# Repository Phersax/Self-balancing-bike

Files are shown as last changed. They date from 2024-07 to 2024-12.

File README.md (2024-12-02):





## About the Project
This project involves the development of a self-balancing bicycle designed to remain stable in
a stationary position on a flat surface. The balance is autonomously maintained through a
reaction wheel powered by a motor, whose controlled movement counteracts the bicycle’s tilt.
For small tilt angles, the system can be approximated as an inverted pendulum.
The structure was created using 3D printing and then assembled, following a preliminary modeling phase in SolidWorks.

The control system relies on precise timing: A main timer manages a callback triggered at
defined time intervals, while a second timer regulates the generation of the PWM signal needed
to control the motor. An additional timer has been set up for reading the encoder data. As for
the data from the IMU, it is acquired via the I2C protocol.

The control model is structured with two loops. The inner loop uses encoder data to implement
closed-loop speed control, while the outer loop relies on IMU readings to adjust the position.
To achieve an accurate angle reading, sensor data fusion has been implemented through a filter
that combines information from an MPU6050 IMU, equipped with an integrated accelerometer
and gyroscope.

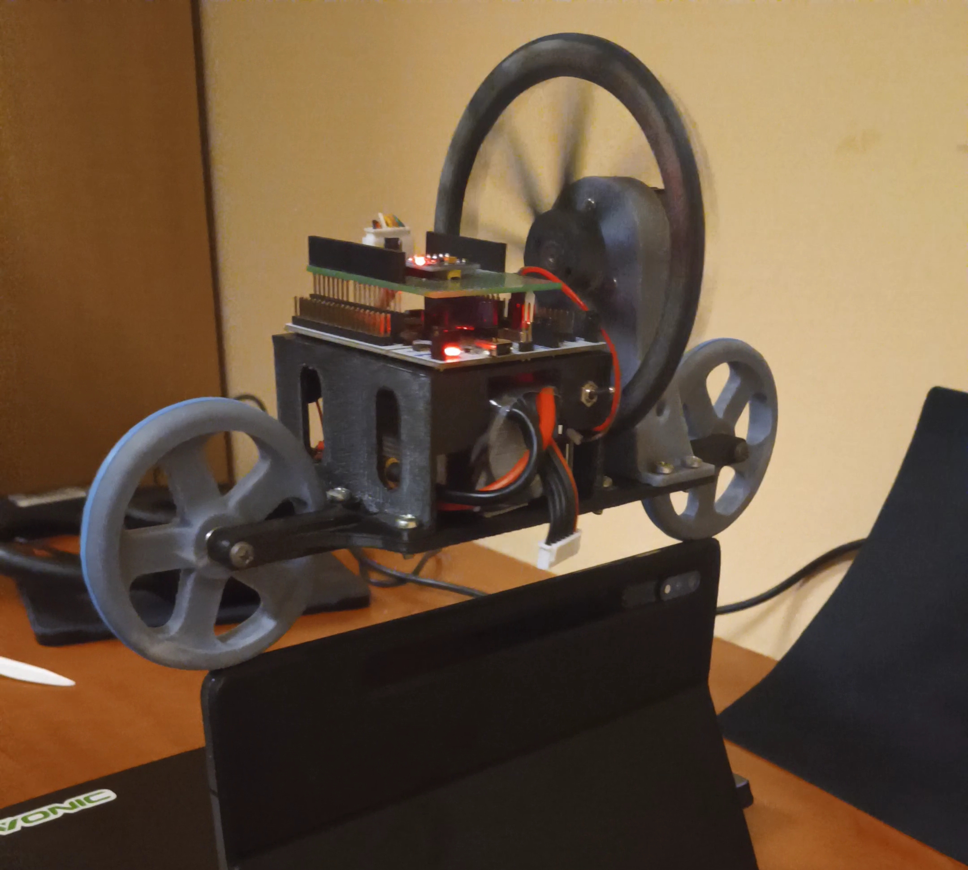
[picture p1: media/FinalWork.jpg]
Final Overview


## Schematic
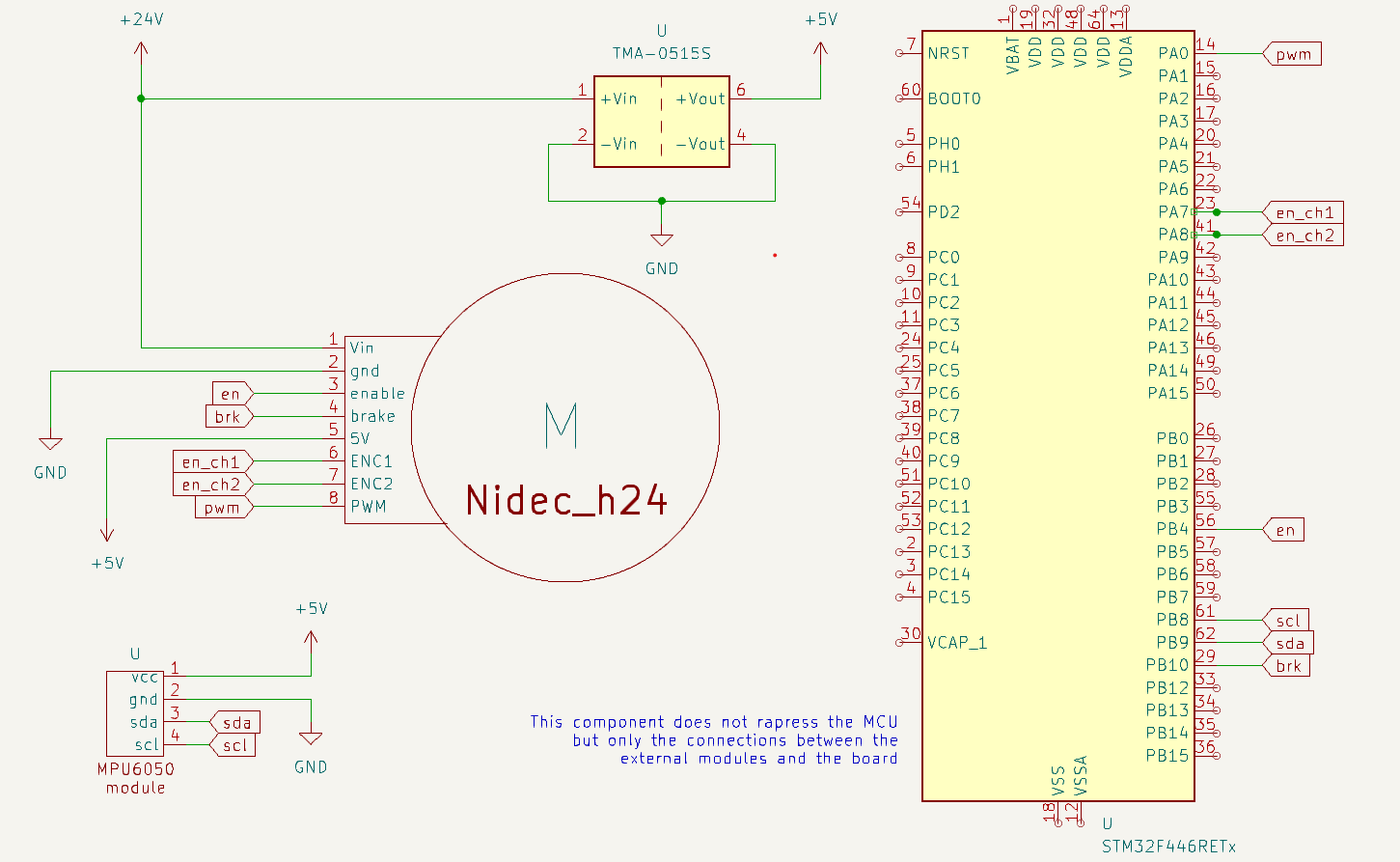
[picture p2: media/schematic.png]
Schematic


## Additional info
Check out the report if you are interested in our work!

[Link to the report](SELF_BALANCING_BIKE_REPORT.pdf)

[Link to the pinout and configuration](pinout_and_config_report.pdf)

🚀 Happy coding! 🌟

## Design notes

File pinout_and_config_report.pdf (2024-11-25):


25/11/2024

main Project
Configuration Report

## 1. Description

### 1.1. Project

Project Name | main
Board Name | custom
Generated with: | STM32CubeMX 6.12.1
Date | 11/25/2024

### 1.2. MCU

MCU Series | STM32F4
MCU Line | STM32F446
MCU name | STM32F446RETx
MCU Package | LQFP64
MCU Pin number | 64

### 1.3. Core(s) information

Core(s) | Arm Cortex-M4

## 2. Pinout Configuration

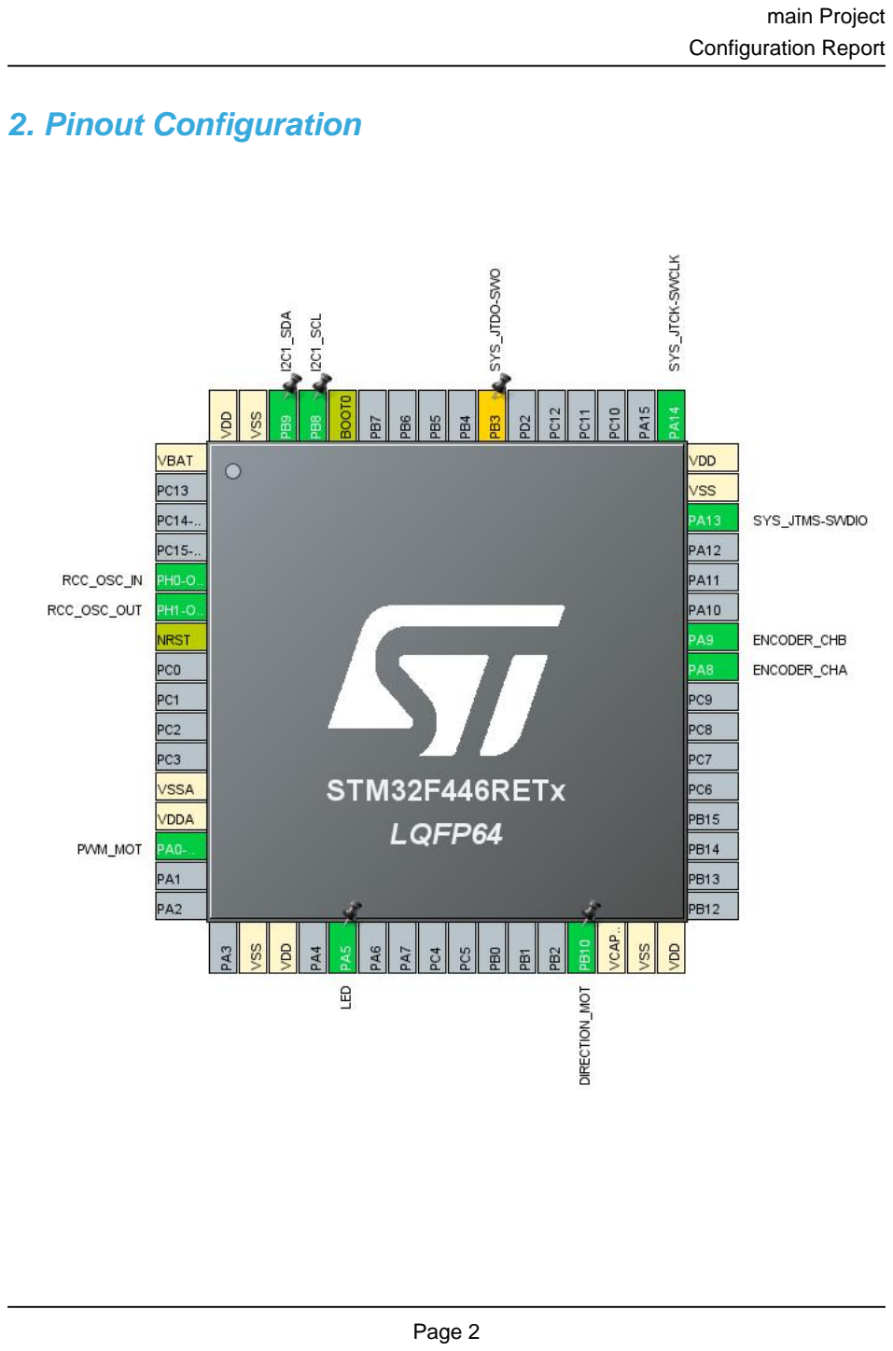
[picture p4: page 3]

## 3. Pins Configuration

Pin Number LQFP64 | Pin Name (function after reset) | Pin Type | Alternate Function(s) | Label
1 | VBAT | Power
5 | PH0-OSC_IN | I/O | RCC_OSC_IN
6 | PH1-OSC_OUT | I/O | RCC_OSC_OUT
7 | NRST | Reset
12 | VSSA | Power
13 | VDDA | Power
14 | PA0-WKUP | I/O | TIM5_CH1 | PWM_MOT
18 | VSS | Power
19 | VDD | Power
21 | PA5 * | I/O | GPIO_Output | LED
29 | PB10 * | I/O | GPIO_Output | DIRECTION_MOT
30 | VCAP_1 | Power
31 | VSS | Power
32 | VDD | Power
41 | PA8 | I/O | TIM1_CH1 | ENCODER_CHA
42 | PA9 | I/O | TIM1_CH2 | ENCODER_CHB
46 | PA13 | I/O | SYS_JTMS-SWDIO
47 | VSS | Power
48 | VDD | Power
49 | PA14 | I/O | SYS_JTCK-SWCLK
55 | PB3 ** | I/O | SYS_JTDO-SWO
60 | BOOT0 | Boot
61 | PB8 | I/O | I2C1_SCL
62 | PB9 | I/O | I2C1_SDA
63 | VSS | Power
64 | VDD | Power

* The pin is affected with an I/O function
** The pin is affected with a peripheral function but no peripheral mode is activated

## 4. Clock Tree Configuration

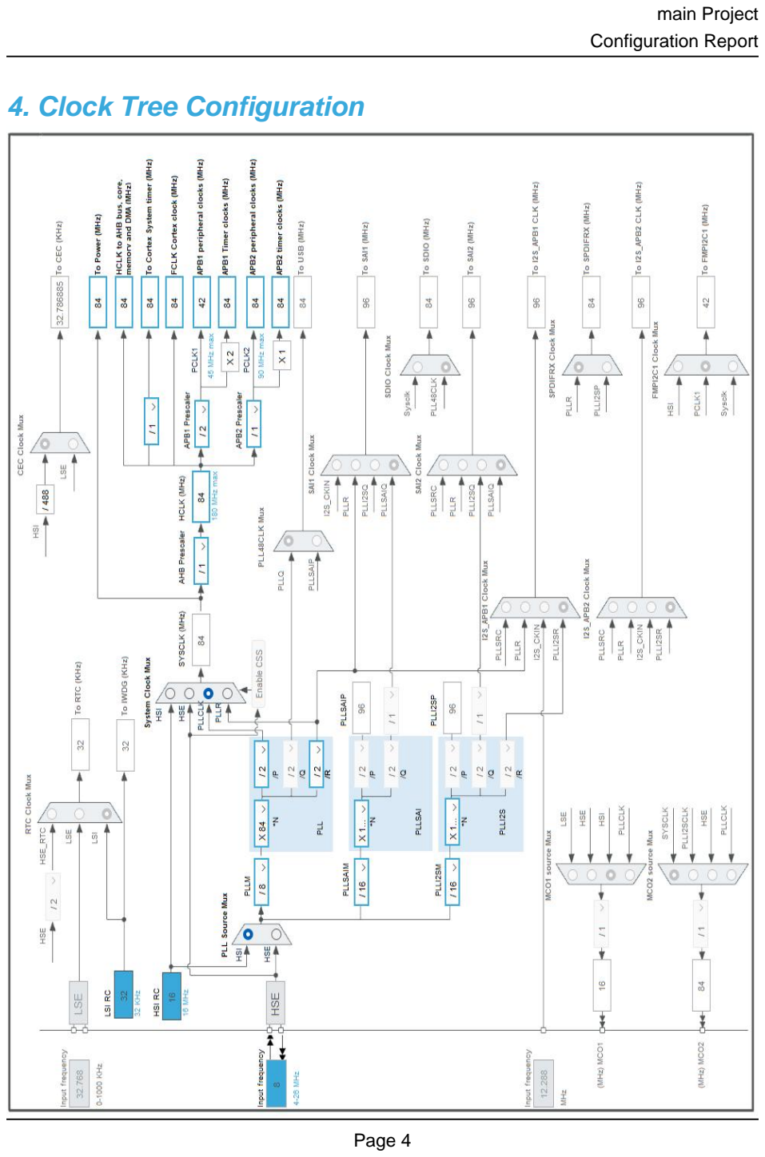
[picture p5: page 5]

## 1. Power Consumption Calculator report

### 1.1. Microcontroller Selection

Series | STM32F4
Line | STM32F446
MCU | STM32F446RETx
Datasheet | DS10693_Rev6

### 1.2. Parameter Selection

Temperature | 25
Vdd | 3.3

### 1.3. Battery Selection

Battery | Li-SOCL2(A3400)
Capacity | 3400.0 mAh
Self Discharge | 0.08 %/month
Nominal Voltage | 3.6 V
Max Cont Current | 100.0 mA
Max Pulse Current | 200.0 mA
Cells in series | 1
Cells in parallel | 1

### 1.4. Sequence

Step | Step1 | Step2
Mode | RUN | STOP_UDM (Under Drive)
Vdd | 3.3 | 3.3
Voltage Source | Battery | Battery
Range | Scale1-High | No Scale
Fetch Type | RAM/FLASH/REGON/ART/P REFETCH | n/a
CPU Frequency | 180 MHz | 0 Hz
Clock Configuration | HSE PLL | Regulator_LP Flash-PwrDwn
Clock Source Frequency | 4 MHz | 0 Hz
Peripherals
Additional Cons. | 0 mA | 0 mA
Average Current | 46 mA | 55 µA
Duration | 0.1 ms | 0.9 ms
DMIPS | 225.0 | 0.0
Ta Max | 98.02 | 104.99
Category | In DS Table | In DS Table

### 1.5. Results

Sequence Time | 1 ms | Average Current | 4.65 mA
Battery Life | 1 month | Average DMIPS | 225.0 DMIPS

### 1.6. Chart

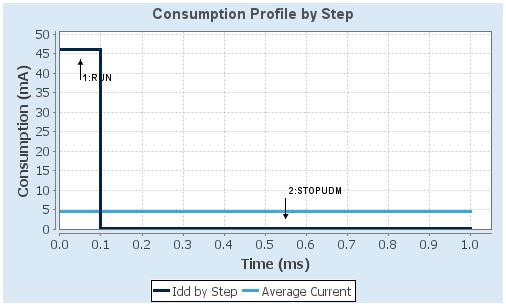
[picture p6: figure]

## 2. Software Project

### 2.1. Project Settings

Name | Value
Project Name | main
Project Folder | C:\Users\Francesco Stasi\OneDrive - Politecnico di
Toolchain / IDE | STM32CubeIDE
Firmware Package Name and Version | STM32Cube FW_F4 V1.28.1
Application Structure | Advanced
Generate Under Root | Yes
Do not generate the main() | No
Minimum Heap Size | 0x200
Minimum Stack Size | 0x400

### 2.2. Code Generation Settings

Name | Value
STM32Cube MCU packages and embedded software | Copy only the necessary library files
Generate peripheral initialization as a pair of '.c/.h' files | Yes
Backup previously generated files when re-generating | No
Keep User Code when re-generating | Yes
Delete previously generated files when not re-generated | Yes
Set all free pins as analog (to optimize the power consumption) | No
Enable Full Assert | No

### 2.3. Advanced Settings - Generated Function Calls

Rank | Function Name | Peripheral Instance Name
1 | SystemClock_Config | RCC
2 | MX_GPIO_Init | GPIO
3 | MX_TIM5_Init | TIM5
4 | MX_I2C1_Init | I2C1
5 | MX_TIM1_Init | TIM1
6 | MX_TIM2_Init | TIM2

## 3. Peripherals and Middlewares Configuration

### 3.1. I2C1

I2C: I2C
3.1.1. Parameter Settings:

Master Features:

I2C Speed Mode | Fast Mode *
I2C Clock Speed (Hz) | 400000
Fast Mode Duty Cycle | Duty cycle Tlow/Thigh = 2
Slave Features:
Clock No Stretch Mode | Disabled
Primary Address Length selection | 7-bit
Dual Address Acknowledged | Disabled
Primary slave address | 0
General Call address detection | Disabled

### 3.2. RCC

High Speed Clock (HSE): Crystal/Ceramic Resonator
3.2.1. Parameter Settings:

System Parameters:

VDD voltage (V) | 3.3
Instruction Cache | Enabled
Prefetch Buffer | Enabled
Data Cache | Enabled
Flash Latency(WS) | 2 WS (3 CPU cycle)
RCC Parameters:
HSI Calibration Value | 16
TIM Prescaler Selection | Disabled
HSE Startup Timout Value (ms) | 100
LSE Startup Timout Value (ms) | 5000
Power Parameters:
Power Regulator Voltage Scale | Power Regulator Voltage Scale 3
Power Over Drive | Disabled

### 3.3. SYS

Debug: Serial Wire
Timebase Source: SysTick

### 3.4. TIM1

Combined Channels: Encoder Mode
3.4.1. Parameter Settings:

Counter Settings:

Prescaler (PSC - 16 bits value) | 0
Counter Mode | Up
Counter Period (AutoReload Register - 16 bits value ) | 65535
Internal Clock Division (CKD) | No Division
Repetition Counter (RCR - 8 bits value) | 0
auto-reload preload | Disable
Trigger Output (TRGO) Parameters:
Master/Slave Mode (MSM bit) | Disable (Trigger input effect not delayed)
Trigger Event Selection | Reset (UG bit from TIMx_EGR)
Encoder:
Encoder Mode | Encoder Mode TI1 and TI2 *

____ Parameters for Channel 1 ____
Polarity | Rising Edge
IC Selection | Direct
Prescaler Division Ratio | No division
Input Filter | 0
____ Parameters for Channel 2 ____
Polarity | Rising Edge
IC Selection | Direct
Prescaler Division Ratio | No division
Input Filter | 0

### 3.5. TIM2

Clock Source : Internal Clock
3.5.1. Parameter Settings:

Counter Settings:

Prescaler (PSC - 16 bits value) | 0
Counter Mode | Up

Counter Period (AutoReload Register - 32 bits value ) | 336000-1 *
Internal Clock Division (CKD) | No Division
auto-reload preload | Disable
Trigger Output (TRGO) Parameters:
Master/Slave Mode (MSM bit) | Disable (Trigger input effect not delayed)
Trigger Event Selection | Reset (UG bit from TIMx_EGR)

### 3.6. TIM5

Channel1: PWM Generation CH1
3.6.1. Parameter Settings:

Counter Settings:

Prescaler (PSC - 16 bits value) | 0
Counter Mode | Up
Counter Period (AutoReload Register - 32 bits value ) | 4199 *
Internal Clock Division (CKD) | No Division
auto-reload preload | Enable *
Trigger Output (TRGO) Parameters:
Master/Slave Mode (MSM bit) | Disable (Trigger input effect not delayed)
Trigger Event Selection | Reset (UG bit from TIMx_EGR)
PWM Generation Channel 1:
Mode | PWM mode 1
Pulse (32 bits value) | 0
Output compare preload | Enable
Fast Mode | Disable
CH Polarity | High

* User modified value

## 4. System Configuration

### 4.1. GPIO configuration

IP | Pin | Signal | GPIO mode | GPIO pull/up pull down | Max Speed | User Label
I2C1 | PB8 | I2C1_SCL | Alternate Function Open Drain | Pull-up * | Very High *
| PB9 | I2C1_SDA | Alternate Function Open Drain | Pull-up * | Very High *
RCC | PH0-OSC_IN | RCC_OSC_IN | n/a | n/a | n/a
| PH1-OSC_OUT | RCC_OSC_OUT | n/a | n/a | n/a
SYS | PA13 | SYS_JTMS-SWDIO | n/a | n/a | n/a
| PA14 | SYS_JTCK-SWCLK | n/a | n/a | n/a
TIM1 | PA8 | TIM1_CH1 | Alternate Function Push Pull | Pull-up * | Low | ENCODER_CHA
| PA9 | TIM1_CH2 | Alternate Function Push Pull | Pull-up * | Low | ENCODER_CHB
TIM5 | PA0-WKUP | TIM5_CH1 | Alternate Function Push Pull | No pull-up and no pull-down | Low | PWM_MOT
Single Mapped Signals | PB3 | SYS_JTDO-SWO | n/a | n/a | n/a
GPIO | PA5 | GPIO_Output | Output Push Pull | No pull-up and no pull-down | Low | LED
| PB10 | GPIO_Output | Output Push Pull | Pull-down * | Low | DIRECTION_MOT

### 4.2. DMA configuration

nothing configured in DMA service

### 4.3. NVIC configuration

4.3.1. NVIC
Interrupt Table | Enable | Preenmption Priority | SubPriority
Non maskable interrupt | true | 0 | 0
Hard fault interrupt | true | 0 | 0
Memory management fault | true | 0 | 0
Pre-fetch fault, memory access fault | true | 0 | 0
Undefined instruction or illegal state | true | 0 | 0
System service call via SWI instruction | true | 0 | 0
Debug monitor | true | 0 | 0
Pendable request for system service | true | 0 | 0
System tick timer | true | 15 | 0
TIM2 global interrupt | true | 0 | 0
PVD interrupt through EXTI line 16 | unused
Flash global interrupt | unused
RCC global interrupt | unused
TIM1 break interrupt and TIM9 global interrupt | unused
TIM1 update interrupt and TIM10 global interrupt | unused
TIM1 trigger and commutation interrupts and TIM11 global interrupt | unused
TIM1 capture compare interrupt | unused
I2C1 event interrupt | unused
I2C1 error interrupt | unused
TIM5 global interrupt | unused
FPU global interrupt | unused
4.3.2. NVIC Code generation
Enabled interrupt Table | Select for init sequence ordering | Generate IRQ handler | Call HAL handler
Non maskable interrupt | false | true | false
Hard fault interrupt | false | true | false
Memory management fault | false | true | false
Pre-fetch fault, memory access fault | false | true | false
Undefined instruction or illegal state | false | true | false
System service call via SWI instruction | false | true | false
Debug monitor | false | true | false
Pendable request for system service | false | true | false
System tick timer | false | true | true
TIM2 global interrupt | false | true | true

* User modified value

## 5. System Views

5.1. Category view
5.1.1. Current

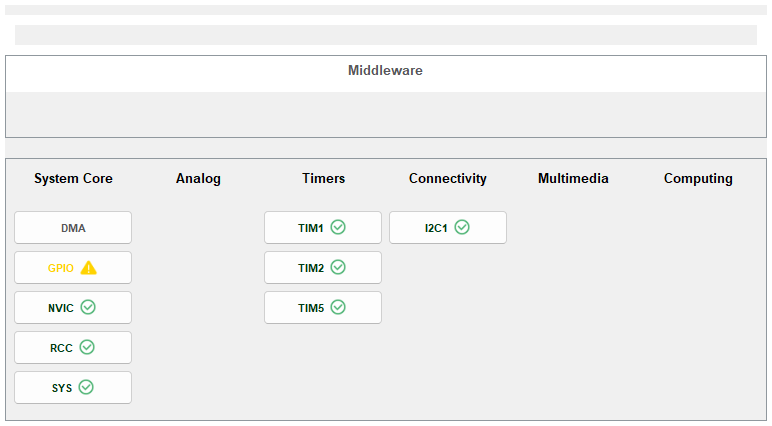
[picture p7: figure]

## 6. Docs & Resources

Type | Link
BSDL files | https://www.st.com/resource/en/bsdl_model/stm32f446_bsdl.zip
IBIS models | https://www.st.com/resource/en/ibis_model/stm32f446_ibis.zip
System View Description | https://www.st.com/resource/en/svd/stm32f4-svd.zip
Presentations | https://www.st.com/resource/en/product_presentation/stm32-stm8_embedded_software_solutions.pdf
Presentations | https://www.st.com/resource/en/product_presentation/stm32_eval-tools_portfolio.pdf
Presentations | https://www.st.com/resource/en/product_presentation/stm32_stm8_functi onal-safety-packages.pdf
Presentations | https://www.st.com/resource/en/product_presentation/stm32-stm8_software_development_tools.pdf
Presentations | https://www.st.com/resource/en/product_presentation/microcontrollers-stm32-family-overview.pdf
Presentations | https://www.st.com/resource/en/product_presentation/microcontrollers-stm32h7rs-lines-overview.pdf
Brochures | https://www.st.com/resource/en/brochure/products-and-solutions-for-plcs-and-smart-i-os.pdf
Flyers | https://www.st.com/resource/en/flyer/flstm32nucleo.pdf
Flyers | https://www.st.com/resource/en/flyer/flstmcsuite.pdf
Flyers | https://www.st.com/resource/en/flyer/flstm32trust.pdf
Product Certifications | https://www.st.com/resource/en/certification_document/stm32_authentication_can.pdf
Application Notes | https://www.st.com/resource/en/application_note/an1709-emc-design-guide-for-stm8-stm32-and-legacy-mcus-stmicroelectronics.pdf
Application Notes | https://www.st.com/resource/en/application_note/an2606-stm32-microcontroller-system-memory-boot-mode-stmicroelectronics.pdf
Application Notes | https://www.st.com/resource/en/application_note/an2639-soldering- recommendations-and-package-information-for-leadfree-ecopack-mcus-

| and-mpus-stmicroelectronics.pdf
Application Notes | https://www.st.com/resource/en/application_note/an2945-stm8s-and-stm32-mcus-a-consistent-832bit-product-line-for-painless-migration-stmicroelectronics.pdf
Application Notes | https://www.st.com/resource/en/application_note/an3070-managing-the-driver-enable-signal-for-rs485-and-iolink-communications-with-the-stm32s-usart-stmicroelectronics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
Application Notes | https://www.st.com/resource/en/application_note/an3126-audio-and-waveform-generation-using-the-dac-in-stm32-products-stmicroelectronics.pdf
Application Notes | https://www.st.com/resource/en/application_note/an3154-can-protocol-used-in-the-stm32-bootloader-stmicroelectronics.pdf
Application Notes | https://www.st.com/resource/en/application_note/an3155-usart-protocol-used-in-the-stm32-bootloader-stmicroelectronics.pdf
Application Notes | https://www.st.com/resource/en/application_note/an3156-usb-dfu-protocol-used-in-the-stm32-bootloader-stmicroelectronics.pdf
Application Notes | https://www.st.com/resource/en/application_note/an3364-migration-and-compatibility-guidelines-for-stm32-microcontroller-applications-stmicroelectronics.pdf
Application Notes | https://www.st.com/resource/en/application_note/an3997-audio-playback-and-recording-using-the-stm32f4discovery-stmicroelectronics.pdf
Application Notes | https://www.st.com/resource/en/application_note/an3998-pdm-audio-software-decoding-on-stm32-microcontrollers-stmicroelectronics.pdf
Application Notes | https://www.st.com/resource/en/application_note/an4031-using-the-stm32f2-stm32f4-and-stm32f7-series-dma-controller-stmicroelectronics.pdf
Application Notes | https://www.st.com/resource/en/application_note/an4221-i2c-protocol-used-in-the-stm32-bootloader-stmicroelectronics.pdf
Application Notes | https://www.st.com/resource/en/application_note/an4229-how-to-implement-a-vocoder-solution-using-stm32-microcontrollers-stmicroelectronics.pdf
Application Notes | https://www.st.com/resource/en/application_note/an4286-spi-protocol-used-in-the-stm32-bootloader-stmicroelectronics.pdf

Application Notes | https://www.st.com/resource/en/application_note/an4488-getting-started-with-stm32f4xxxx-mcu-hardware-development-stmicroelectronics.pdf
Application Notes | https://www.st.com/resource/en/application_note/an4566-extending-the-dac-performance-of-stm32-microcontrollers-stmicroelectronics.pdf
Application Notes | https://www.st.com/resource/en/application_note/an4640-peripherals-interconnections-on-stm32f4057xx-stm32f4157xx-stm32f42xxx-stm32f43xxx-stm32f446xx-and-stm32f469479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
Application Notes | https://www.st.com/resource/en/application_note/an4655-virtually-increasing-the-number-of-serial-communication-peripherals-in-stm32-applications-stmicroelectronics.p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
Application Notes | https://www.st.com/resource/en/application_note/an4658-migration-of-applications-from-stm32f429439-lines-to-stm32f446-line-stmicroelectronics.pdf
Application Notes | https://www.st.com/resource/en/application_note/an4739-stm32cube-firmware-examples-for-stm32f4-series-stmicroelectronics.pdf
Application Notes | https://www.st.com/resource/en/application_note/an4750-handling-of-soft-errors-in-stm32-applications-stmicroelectronics.pdf
Application Notes | https://www.st.com/resource/en/application_note/an4776-generalpurpose-timer-cookbook-for-stm32-microcontrollers-stmicroelectronics.pdf
Application Notes | https://www.st.com/resource/en/application_note/an4803-highspeed-si-simulations-using-ibis-and-boardlevel-simulations-using-hyperlynx-si-on-stm32-mcus-and-mpus-stmic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
Application Notes | https://www.st.com/resource/en/application_note/an4850-stm32-mcus-spreadspectrum-clock-generation-principles-properties-and-implementation-stmicroelectronics.pdf
Application Notes | https://www.st.com/resource/en/application_note/an4989-stm32-microcontroller-debug-toolbox-stmicroelectronics.pdf
Application Notes | https://www.st.com/resource/en/application_note/an4995-using-an-electromyogram-technique-to-detect-muscle-activity-stmicroelectronics.pdf
Application Notes | https://www.st.com/resource/en/application_note/an5020-digital-camera-interface-dcmi-on-stm32-mcus-stmicroelectronics.pdf
Application Notes | https://www.st.com/resource/en/application_note/an5027-interfacing-pdm-

| digital-microphones-using-stm32-mcus-and-mpus-stmicroelectronics.pdf
Application Notes | https://www.st.com/resource/en/application_note/an5073-receiving-spdif-audio-stream-with-the-stm32f4f7h7-series-stmicroelectronics.pdf
Application Notes | https://www.st.com/resource/en/application_note/an4760-quadspi-interface-on-stm32-microcontrollers-and-microprocessors--stmicroelectronics.pdf
Application Notes | https://www.st.com/resource/en/application_note/an4899-stm32-microcontroller-gpio-hardware-settings-and-lowpower-consumption-stmicroelectronics.pdf
Application Notes | https://www.st.com/resource/en/application_note/an5612-esd-protection-of-stm32-mcus-and-mpus-stmicroelectronics.pdf
Application Notes | https://www.st.com/resource/en/application_note/an4838-introduction-to-memory-protection-unit-management-on-stm32-mcus-stmicroelectronics.pdf
Application Notes | https://www.st.com/resource/en/application_note/an4879-introduction-to-usb-hardware-and-pcb-guidelines-using-stm32-mcus-stmicroelectronics.pdf
Application Notes | https://www.st.com/resource/en/application_note/an5225-introduction-to-usb-typec-power-delivery-for-stm32-mcus-and-mpus-stmicroelectronics.pdf
Application Notes | https://www.st.com/resource/en/application_note/an2834-how-to-optimize-the-adc-accuracy-in-the-stm32-mcus-stmicroelectronics.pdf
Application Notes | https://www.st.com/resource/en/application_note/an5537-how-to-use-adc-oversampling-techniques-to-improve-signaltonoise-ratio-on-stm32-mcus-stmicroelectronics.pdf
Application Notes | https://www.st.com/resource/en/application_note/an5036-guidelines-for-thermal-management-on-stm32-applications-stmicroelectronics.pdf
Application Notes | https://www.st.com/resource/en/application_note/an4230-introduction-to-random-number-generation-validation-using-the-nist-statistical-test-suite-for-stm32-mcus-and-m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
Application Notes | https://www.st.com/resource/en/application_note/an2867-guidelines-for-oscillator-design-on-stm8afals-and-stm32-mcusmpus-stmicroelectronics.pdf

Application Notes | https://www.st.com/resource/en/application_note/an4013-introduction-to-timers-for-stm32-mcus-stmicroelectronics.pdf
Application Notes | https://www.st.com/resource/en/application_note/an4277-how-to-use-pwm-shutdown-for-motor-control-and-digital-power-conversion-on-stm32-mcus-stmicroelectronics.pdf
Application Notes | https://www.st.com/resource/en/application_note/an4759-introduction-to-using-the-hardware-realtime-clock-rtc-and-the-tamper-management-unit-tamp-with-stm32-mcus-stmi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
Application Notes | https://www.st.com/resource/en/application_note/an4908-getting-started-with-usart-automatic-baud-rater-detection-for-stm32-mcus-stmicroelectronics.pdf
Application Notes | https://www.st.com/resource/en/application_note/an5156-introduction-to-security-for-stm32-mcus-stmicroelectronics.pdf
Application Notes | https://www.st.com/resource/en/application_note/an5543-guidelines-for-enhanced-spi-communication-on-stm32-mcus-and-mpus-stmicroelectronics.pdf
Application Notes | https://www.st.com/resource/en/application_note/an5992-migrating-from-stm32f446-to-stm32h523533-mcus-stmicroelectronics.pdf
Application Notes for related Tools & Software | https://www.st.com/resource/en/application_note/an1202_freertos_guide-freertos-guide-stmicroelectronics.pdf
Application Notes for related Tools & Software | https://www.st.com/resource/en/application_note/an1602_semihosting_in_truestudio-how-to-do-semihosting-in-truestudio-stmicroelectronics.pdf
Application Notes for related Tools & Software | https://www.st.com/resource/en/application_note/an1801_stm32cubeprogrammer_in_truestudio-installing-stm32cubeprogrammer-in-truestudio-stmicroelectronics.pdf
Application Notes for related Tools & Software | https://www.st.com/resource/en/application_note/atollic_editing_keyboard_shortcuts-atollic-editing-keyboard-shortcuts-stmicroelectronics.pdf
Application Notes for related Tools & Software | https://www.st.com/resource/en/application_note/iar_to_atollic_truestudio_migration_guide-truestudio-for-arm-migration-guide-iar-embedded-workbench-to-truestudio-stm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
Application Notes | https://www.st.com/resource/en/application_note/stm32cubemx_installatio

for related Tools & Software | n_in_truestudio-stm32cubemx-installation-in-truestudio-stmicroelectronics.pdf
Application Notes for related Tools & Software | https://www.st.com/resource/en/application_note/an2656-stm32f10xxx-lcd-glass-driver-firmware-stmicroelectronics.pdf
Application Notes for related Tools & Software | https://www.st.com/resource/en/application_note/an2790-tft-lcd-interfacing-with-the-highdensity-stm32f10xxx-fsmc-stmicroelectronics.pdf
Application Notes for related Tools & Software | https://www.st.com/resource/en/application_note/an3078-stm32-inapplication-programming-over-the-ic-bus-stmicroelectronics.pdf
Application Notes for related Tools & Software | https://www.st.com/resource/en/application_note/an3116-stm32s-adc-modes-and-their-applications-stmicroelectronics.pdf
Application Notes for related Tools & Software | https://www.st.com/resource/en/application_note/an3174-implementing-receivers-for-infrared-remote-control-protocols-using-stm32f10xxx-microcontrollers-stmicroelectro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
Application Notes for related Tools & Software | https://www.st.com/resource/en/application_note/an3241-qvga-tftlcd-direct-drive-using-the-stm32f10xx-fsmc-peripheral-stmicroelectronics.pdf
Application Notes for related Tools & Software | https://www.st.com/resource/en/application_note/an3307-guidelines-for-obtaining-iec-60335-class-b-certification-for-any-stm32-application-stmicroelectronics.pdf
Application Notes for related Tools & Software | https://www.st.com/resource/en/application_note/an3965-stm32f40xstm32f41x-inapplication-programming-using-the-usart-stmicroelectronics.pdf
Application Notes for related Tools & Software | https://www.st.com/resource/en/application_note/an3969-eeprom-emulation-in-stm32f40xstm32f41x-microcontrollers-stmicroelectronics.pdf
Application Notes for related Tools & Software | https://www.st.com/resource/en/application_note/an4044-floating-point-unit-demonstration-on-stm32-microcontrollers-stmicroelectronics.pdf

Application Notes
for related Tools

https://www.st.com/resource/en/application_note/an4323-getting-startedwith-stemwin-library-stmicroelectronics.pdf

& Software
Application Notes for related Tools & Software | https://www.st.com/resource/en/application_note/an4365-using-stm32f4-mcu-power-modes-with-best-dynamic-efficiency-stmicroelectronics.pdf
Application Notes for related Tools & Software | https://www.st.com/resource/en/application_note/an4435-guidelines-for-obtaining-ulcsaiec-607301603351-class-b-certification-in-any-stm32-application-stmicroelectroni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
Application Notes for related Tools & Software | https://www.st.com/resource/en/application_note/an4457-implementing-an-emulated-uart-on-stm32f4-microcontrollers-stmicroelectronics.pdf
Application Notes for related Tools & Software | https://www.st.com/resource/en/application_note/an4499-stm32--nrf51822-bluetooth-low-energy-system-solution-stmicroelectronics.pdf
Application Notes for related Tools & Software | https://www.st.com/resource/en/application_note/an4657-stm32-inapplication-programming-iap-using-the-usart-stmicroelectronics.pdf
Application Notes for related Tools & Software | https://www.st.com/resource/en/application_note/an4666-parallel-synchronous-transmission-using-gpio-and-dma-stmicroelectronics.pdf
Application Notes for related Tools & Software | https://www.st.com/resource/en/application_note/an4678-full-duplex-spi-emulation-for-stm32f4-microcontrollers-stmicroelectronics.pdf
Application Notes for related Tools & Software | https://www.st.com/resource/en/application_note/an4701-proprietary-code-readout-protection-on-microcontrollers-of-the-stm32f4-series-stmicroelectronics.pdf
Application Notes for related Tools & Software | https://www.st.com/resource/en/application_note/an4739-stm32cube-firmware-examples-for-stm32f4-series-stmicroelectronics.pdf
Application Notes for related Tools & Software | https://www.st.com/resource/en/application_note/an4758-proprietary-code-readout-protection-on-stm32l4-stm32l4-stm32g4-and-stm32wb-series-mcus-stmicroelectronics.pdf
Application Notes for related Tools & Software | https://www.st.com/resource/en/application_note/an4841-digital-signal-processing-for-stm32-microcontrollers-using-cmsis-stmicroelectronics.pdf

Application Notes for related Tools & Software | https://www.st.com/resource/en/application_note/an4852-programming-an-external-flash-memory-using-the-uart-bootloader-builtin-stm32-microcontrollers-stmicroelectroni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
Application Notes for related Tools & Software | https://www.st.com/resource/en/application_note/an4968-proprietary-code-read-out-protection-pcrop-on-stm32f72xxx-and-stm32f73xxx-microcontrollers-stmicroelectronics.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
Application Notes for related Tools & Software | https://www.st.com/resource/en/application_note/an5056-integration-guide-for-the-xcubesbsfu-stm32cube-expansion-package-stmicroelectronics.pdf
Application Notes for related Tools & Software | https://www.st.com/resource/en/application_note/an5360-getting-started-with-projects-based-on-the-stm32mp1-series-in-stm32cubeide-stmicroelectronics.pdf
Application Notes for related Tools & Software | https://www.st.com/resource/en/application_note/an5361-getting-started-with-projects-based-on-dualcore-stm32h7-microcontrollers-in-stm32cubeide-stmicroelectronics.pd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
Application Notes for related Tools & Software | https://www.st.com/resource/en/application_note/an5394-getting-started-with-projects-based-on-the-stm32l5-series-in-stm32cubeide-stmicroelectronics.pdf
Application Notes for related Tools & Software | https://www.st.com/resource/en/application_note/an5418-how-to-build-a-simple-usbpd-sink-application-with-stm32cubemx-stmicroelectronics.pdf
Application Notes for related Tools & Software | https://www.st.com/resource/en/application_note/an5426-migrating-graphics-middleware-projects-from-stm32cubemx-540-to-stm32cubemx-550-stmicroelectronics.pdf
Application Notes for related Tools & Software | https://www.st.com/resource/en/application_note/an5464-position-control-of-a-threephase-permanent-magnet-motor-using-xcubemcsdk-or-xcubemcsdkful-stmicroelectronics.p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
Application Notes for related Tools & Software | https://www.st.com/resource/en/application_note/an5564-getting-started-with-projects-based-on-dualcore-stm32wl-microcontrollers-in-stm32cubeide-stmicroelectronics.pd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
Application Notes for related Tools & Software | https://www.st.com/resource/en/application_note/an5698-adapting-the-xcubestl-functional-safety-package-for-stm32-iec-61508-compliant-to-other-safety-standards-stmicr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
Application Notes | https://www.st.com/resource/en/application_note/an5731-stm32cubemx-

for related Tools & Software | and-stm32cubeide-threadsafe-solution-stmicroelectronics.pdf
Application Notes for related Tools & Software | https://www.st.com/resource/en/application_note/an4502-stm32-smbuspmbus-expansion-package-for-stm32cube-stmicroelectronics.pdf
Application Notes for related Tools & Software | https://www.st.com/resource/en/application_note/an5952-how-to-use-cmake-in-stm32cubeide-stmicroelectronics.pdf
Application Notes for related Tools & Software | https://www.st.com/resource/en/application_note/an5054-how-to-perform-secure-programming-using-stm32cubeprogrammer-stmicroelectronics.pdf
Errata Sheets | https://www.st.com/resource/en/errata_sheet/es0298-stm32f446xcxe-device-errata-stmicroelectronics.pdf
Datasheet | https://www.st.com/resource/en/datasheet/dm00141306.pdf
Programming Manuals | https://www.st.com/resource/en/programming_manual/pm0214-stm32-cortexm4-mcus-and-mpus-programming-manual-stmicroelectronics.pdf
Reference Manuals | https://www.st.com/resource/en/reference_manual/rm0390-stm32f446xx-advanced-armbased-32bit-mcus-stmicroelectronics.pdf
Technical Notes & Articles | https://www.st.com/resource/en/technical_note/tn0516-overview-of-the-stm32f0xf100xxf103xx-and-stm32f2xxf30xf4xx-mcus-pmsm-singledual-foc-sdk-v40-stmicroelectronics.p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
Technical Notes & Articles | https://www.st.com/resource/en/technical_note/tn1163-description-of-wlcsp-for-microcontrollers-and-recommendations-for-its-use-stmicroelectronics.pdf
Technical Notes & Articles | https://www.st.com/resource/en/technical_note/tn1204-tape-and-reel-shipping-media-for-stm32-microcontrollers-in-bga-packages-stmicroelectronics.pdf
Technical Notes & Articles | https://www.st.com/resource/en/technical_note/tn1205-tape-and-reel-shipping-media-for-stm8-and-stm32-microcontrollers-in-fpn-packages-stmicroelectronics.pdf
Technical Notes & Articles | https://www.st.com/resource/en/technical_note/tn1206-tape-and-reel-shipping-media-for-stm8-and-stm32-microcontrollers-in-qfp-packages-stmicroelectronics.pdf

Technical Notes & Articles | https://www.st.com/resource/en/technical_note/tn1207-tape-and-reel-shipping-media-for-stm8-and-stm32-microcontrollers-in-so-packages-stmicroelectronics.pdf
Technical Notes & Articles | https://www.st.com/resource/en/technical_note/tn1208-tape-and-reel-shipping-media-for-stm8-and-stm32-microcontrollers-in-tssop-and-ssop-packages-stmicroelectronics.p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
Technical Notes & Articles | https://www.st.com/resource/en/technical_note/tn1433-reference-device-marking-schematics-for-stm32-microcontrollers-and-microprocessors-stmicroelectronics.pdf
Technical Notes & Articles | https://www.st.com/resource/en/technical_note/tn1489-security-bulletin-tn1489stpsirt-physical-attacks-on-stm32-and-stm32cube-firmware-stmicroelectronics.pdf

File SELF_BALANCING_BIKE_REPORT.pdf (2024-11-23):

### SELF-BALANCING BIKE

### Embedded Control Course - A.Y. 2023/2024

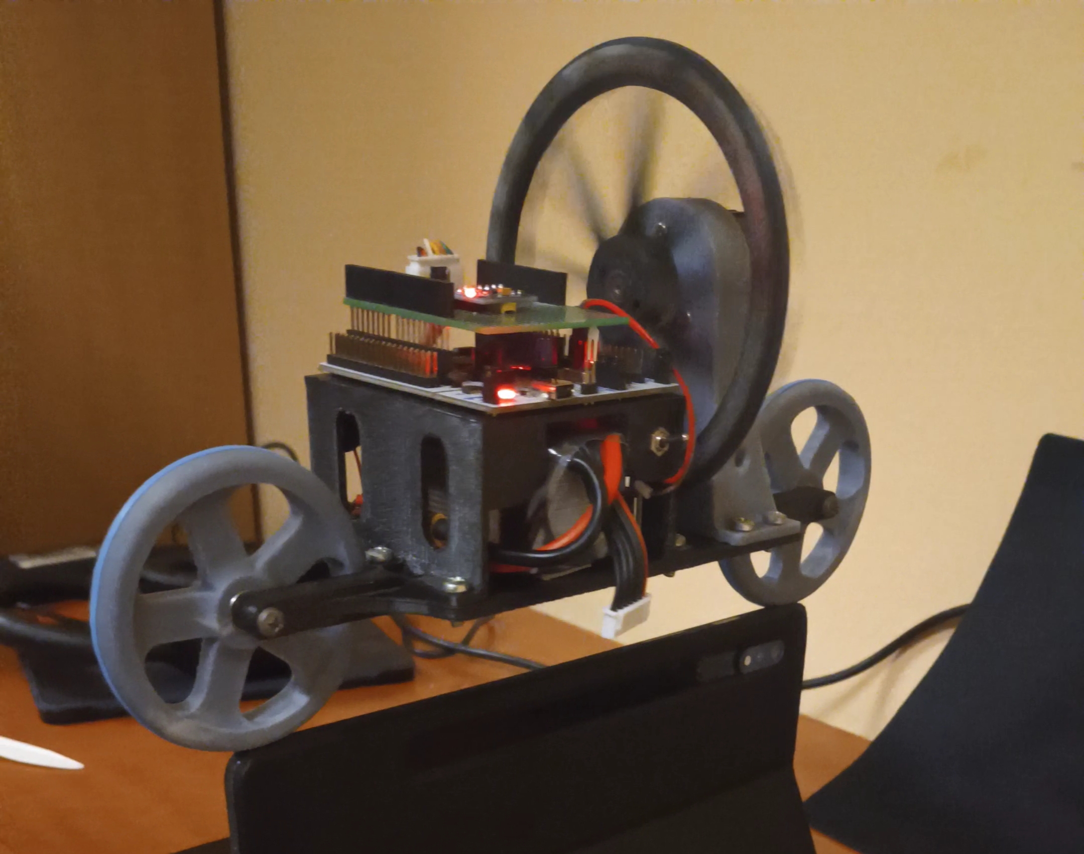
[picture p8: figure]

### Submitted by: Group STmVZ

Group Members:
STASI Francesco, TONTI Davide, VATINNO Simona, ZITO Giovanni

Advisor: Prof. Eng. PhD. DE CICCO Luca

# Contents

1 Introduction | 3
2 Selected Hardware | 4
3 Printed Parts | 10
4 Wirings | 14
5 System’s control | 16
6 The most important parts of the Code | 19
7 Tests and Results | 23

1

8 Conclusions and future developments | 28

# 1 Introduction

This project involves the development of a self-balancing bicycle designed to remain stable in a stationary position on a flat surface. The balance is autonomously maintained through a reaction wheel powered by a motor, whose controlled movement counteracts the bicycle’s tilt. For small tilt angles, the system can be approximated as an inverted pendulum.

The structure was created using 3D printing and then assembled, following a preliminary modeling phase in SolidWorks.

The control system relies on precise timing: A main timer manages a callback triggered at defined time intervals, while a second timer regulates the generation of the PWM signal needed to control the motor. An additional timer has been set up for reading the encoder data. As for the data from the IMU, it is acquired via the I2C protocol.

The control model is structured with two loops. The inner loop uses encoder data to implement closed-loop speed control, while the outer loop relies on IMU readings to adjust the position.

To achieve an accurate angle reading, sensor data fusion has been implemented through a filter that combines information from an MPU6050 IMU, equipped with an integrated accelerometer and gyroscope.

3

# 2 Selected Hardware

This chapter lists and briefly describes the hardware used for our scope.

## 2.1 STM32 NUCLEO-F446RE Overview

The STM32 NUCLEO-F446RE (fig.2.1) is an advanced microcontroller from the STM32 family, built around an ARM Cortex-M4 32-bit core. Operating at frequencies of up to 180 MHz and equipped with a floating-point unit (FPU), it is designed to handle applications requiring high computational performance. With extended support for Digital Signal Processing (DSP)

instructions, this microcontroller is ideal for tasks such as motor control, signal processing, and other advanced embedded applications.

It features 512 KB of flash memory for stable program storage and 128 KB of SRAM for dynamic data management during runtime. Its high-performance clock system ensures precision and efficiency even under demanding workloads. The configurable GPIO ports allow seamless interfacing with external devices such as sensors and actuators, making it highly versatile for various applications.

The STM32 NUCLEO-F446RE integrates a comprehensive set of peripherals, including 12-bit ADC and DAC for analog signal management, advanced timers for precise motor control and PWM generation, and communication interfaces such as I²C, SPI, USART, CAN, and USB

2.0 Full-Speed. Additionally, the DMA (Direct Memory Access) controller enables direct data

transfers between memory and peripherals, reducing CPU load and improving overall performance.

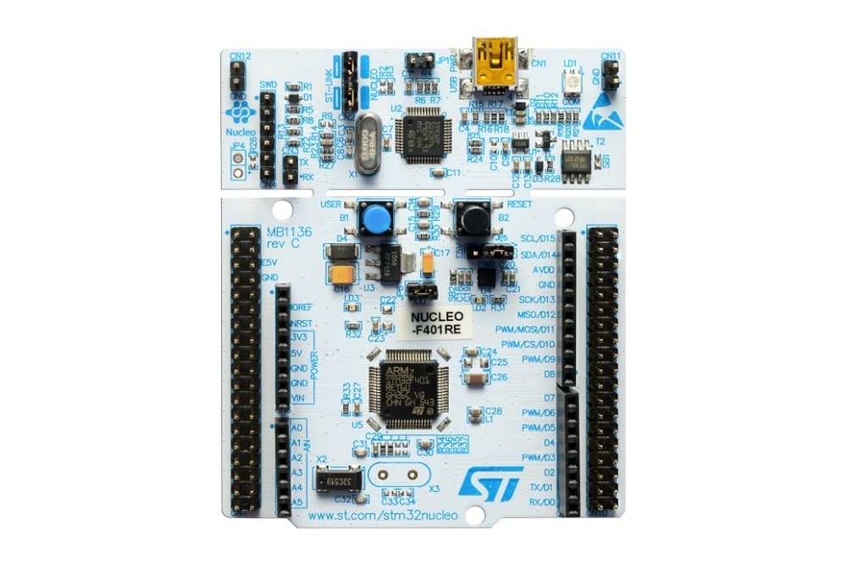
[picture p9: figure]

Figure 2.1: STM32 NUCLEO-F446RE

4

## 2.2 Motor

We choose the Nidec H24 (fig.2.2), a brushless DC motor with 3 phases and 12 poles. It has

a built-in electronic speed driver, that enables an easy control of the speed and direction of the motor, as well as its braking. In addition, it is quite small, compact and light, which is useful for the use case. Its contribution, along with the inertial wheel, guarantees an adequate output torque to balance the bike. It comes with a built-in rotary encoder, to decode its velocity and position.

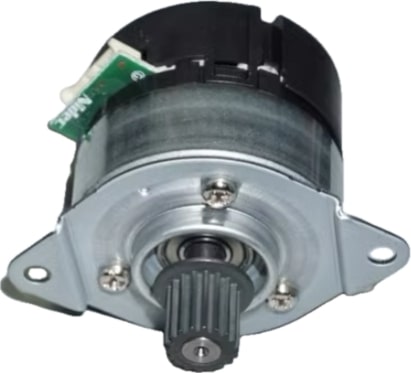
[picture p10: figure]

Figure 2.2: Motor

When powered with 24V, the no-load current is 110mA and the speed is about 6100 rpm.

### 2.2.1 PWM Configuration

The PWM signal was generated with Timer 5 on Channel 1 in output mode. Its frequency was selected according to the specifications of the motor.

PSC ARR | fCLK | fPWM
TIM5 | 0 | 4199 | 84 MHz | 20 kHz

Table 2.1: Configuration of timer 5

Where the frequency was obtained according to the following formula:

1 fPWM | =

(1 + ARR) · (1 + P SC)

| | | fCLK

(2.1)

## 2.3 Encoder

The motor itself is provided with a dual channel phase-tracking encoder (fig.2.3), which allowed

us to discriminate the rotation direction and to determine the velocity of the shaft. It provides 100 PPR and 400 CPR.

Figure 2.3: Motor encoder

### 2.3.1 Encoder Configuration

The encoder was configured to work on Timer 1, where Channel 1 was associated to Channel A and Channel 2 to Channel B. We used the Quadrature Encoder Interface to generate the two square waves.

PSC | ARR | fCLK | fTIM
TIM1 | 0 | 65535 84 MHz | 1.3 kHz

Table 2.2: Configuration of the timer 1

The output frequency of an encoder is a function of the angular velocity of the motor shaft and of the number of divisions of the disk; it can be computed as:

frequency = RPM
60
- Number of divisions of the disk | (2.2)

Consequently, its maximum frequency is 10.2kHz (period of 0.0984ms), which a maximum

velocity of 6100 RPM and 100 divisions of the disk.

## 2.4 Inertial Measurement Unit

The MPU6050 (fig.2.4) sensor module is a comprehensive 6-axis motion tracking device. It

integrates a 3-axis gyroscope, a 3-axis accelerometer, a Digital Motion Processor and an onchip temperature sensor. The communication with microcontrollers is achieved via an I2C bus interface.
The gyroscope was calibrated by summing a series of 1000 readings and then computing their mean. Then, the result was subtracted from the raw readout, before the scaling.

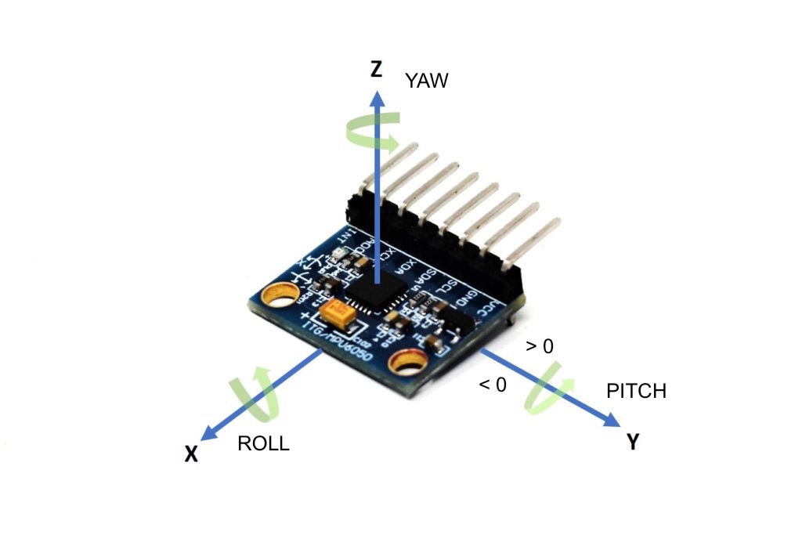
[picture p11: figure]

Figure 2.4: IMU MPU6050

The angles were computed using trigonometric formulas based on the accelerometer’s readings:

pitch = 180
π
- atan2
accelX,

p
accelY² + accelZ²
(2.3)

roll = 180
π
- atan2
accelY,

p
accelX² + accelZ²
(2.4)

### 2.4.1 IMU Communication

We configured the I2C1 of the board in fast mode (i.e. with a frequency of 400 kHz ) and with two GPIO pins associated to SDA and SCL configured as alternate function, that were connected to the sensor.

### 2.4.2 Sensor Fusion

Firstly, the complementary filter was employed to obtain the sensor fusion between accelerometer and gyroscope. More specifically, the gyroscope’s readings have been high pass filtered, while the accelerometer’s readouts were low pass filtered:

currentAngle = α · (previousAngle + gyroAngle) + (1 − α) · accAngle | (2.5)
gyroAngle = gyroReading · Ts | (2.6)

where α was set to 0.98. The filter has been used to eliminate the tendency of drift of the gyroscope and to decrease the noise that comes from the accelerometer.

Then, we used the Kalman filter to smooth the variations and make the response faster, achieving a higher performance. As a matter of fact, the complementary filter offers a straightforward approach but involves a trade-off: you can achieve either a well-smoothed signal with notable delay and reduced amplitude or a signal with minimal delay and accurate amplitude tracking, though at the cost of considerable noise.
To address these limitations, the Kalman filter provides a more advanced alternative. It predicts the next value by leveraging knowledge of the system’s model or the expected pattern of signal changes.
The following table shows the advantages of using the two filters:
Complementary Filter | Kalman Filter
Simplicity | Handling unreliable measure-ments
Speed of computation | Adaptability to system changes
Stable and reliable in real-worlds conditions | Ability to predict future system states
| Adaptability to complex dynamic models

Table 2.3: Filters advantages

The Kalman filter’s predictive capabilities stem from its two-phase operation: prediction and update. During the prediction phase, the next state is estimated using the system’s dynamics, as implemented in the following code:

Listing 2.1: Prediction phase

1 | k -> angle += DT_k * input ; // State prediction based on input
2 | k -> uncertainty += PROCESS_NOISE ; // Increase uncertainty due to model noise

Here, the angle is updated based on the input, scaled by the sampling interval DT k. The uncertainty is increased to incorporate the process noise.
In the update phase, the Kalman filter refines this prediction using the new measurement, combining it with the prediction to minimize uncertainty. This is achieved through the computation of the Kalman gain and the correction of the prediction:

Listing 2.2: Update phase

1 | k -> kalmanGain = k -> uncertainty / (k - > uncertainty + MEASURE_NOISE ); // Calculate Kalman gain
2 | k -> angle += k -> kalmanGain * ( measurement - k -> angle ) ; // Correct prediction using measurement
3 | k -> uncertainty = (1 - k -> kalmanGain ) * k -> uncertainty ; // Update uncertainty

The Kalman gain dynamically adjusts the weighting of the predicted state and the measurement, favoring the more reliable source. This iterative prediction process allows the Kalman filter to adapt to varying conditions, such as sensor noise levels or rapid changes in system dynamics. By continuously updating the state and considering uncertainty, it provides real-time performance improvements that are particularly valuable for applications like the sensor fusion of an IMU (MPU6050), where precise and stable data is crucial to guarantee the balancing.

## 2.5 Power Supply

Lithium-polymeric batteries (fig. 2.6) are rechargeable batteries that have about four times

the energy of other kinds of accumulator. LiPo batteries are lighter and more flexible than other kinds of lithium-ion batteries because of their soft shells, allowing them to be used in mobile and other electronic devices. We used it along with its charger. It provides 22.2V and 1300mAh.

A DC-DC buck converter (fig.2.5) is a type of switch-mode power supply that steps down a higher DC input voltage (22.2V in our case) to a lower output voltage (i.e. 5V).

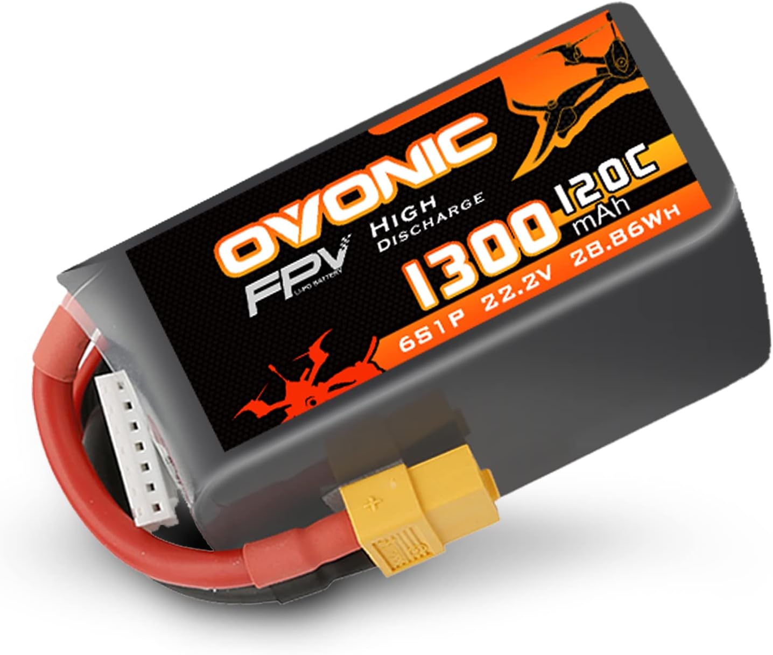
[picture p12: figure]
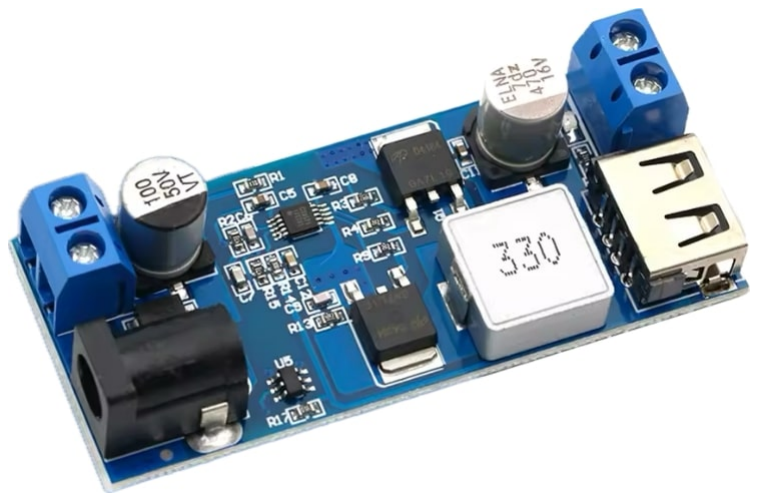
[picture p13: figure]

Figure 2.5: DC-DC buck converter | Figure 2.6: Lipo battery

# 3 Printed Parts

## 3.1 3D model design

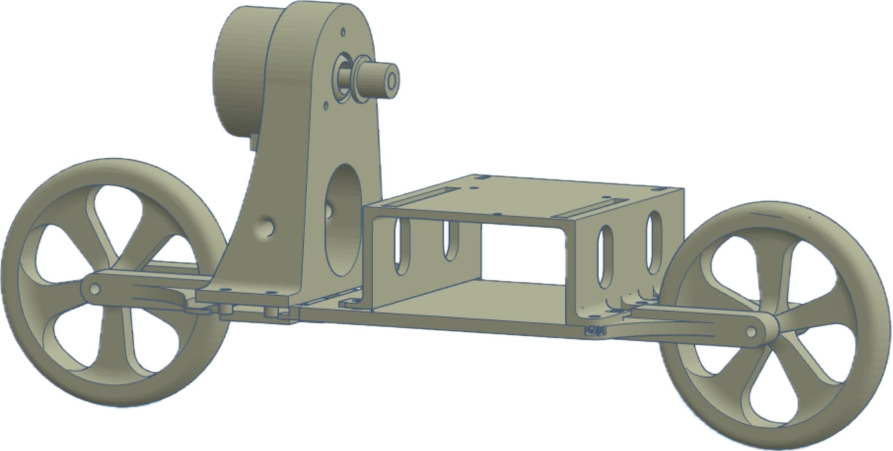
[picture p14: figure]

Figure 3.1: 3d model Solidworks

The 3D model (fig.3.1) was created using SolidWorks [2]. The structure had to be designed

considering the weight and dimensions of the various components. Once the model was completed with all the parts, the software allowed for an accurate calculation of the structure’s center of gravity.

Compared to similar projects, the use of a board like the STM32F446RE required a wider and taller overall structure. All parts was subsequently printed in PLA, ABS, or resin, and prepared for final assembly.

10

## 3.2 Motor Support

The support (fig.3.2) is meant to hold the motor in place and to group and organize the cables

through a hole on its side.

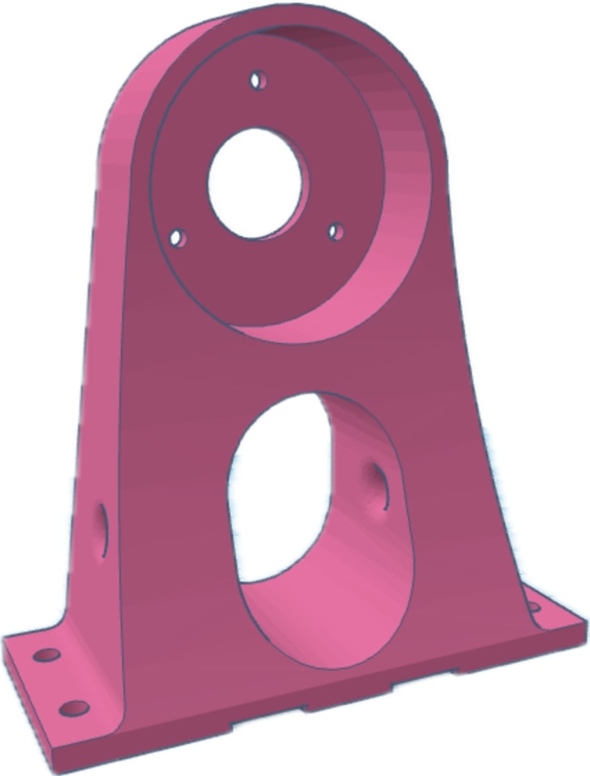
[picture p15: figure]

Figure 3.2: 3D printed bike

## 3.3 Wheels

The wheel (fig.3.3) is the load-bearing turn on which the bike will have to balance, with a bearing inside (fig.3.4) to accomodate the shaft.

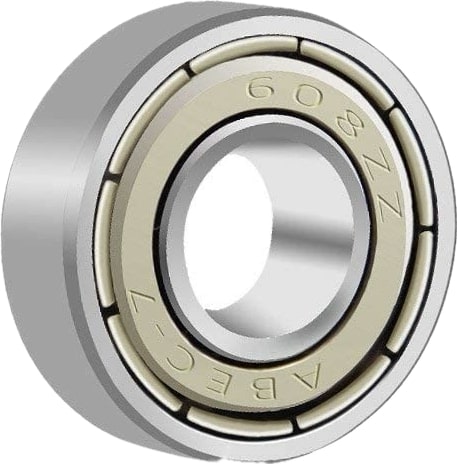
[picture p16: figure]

Figure 3.3: Wheel | Figure 3.4: Bearing

Figure 3.5: Wheel and bearing

## 3.4 Frame Part

The frame (fig.3.6) it’s the main weight-bearing structure, where all the components are placed.

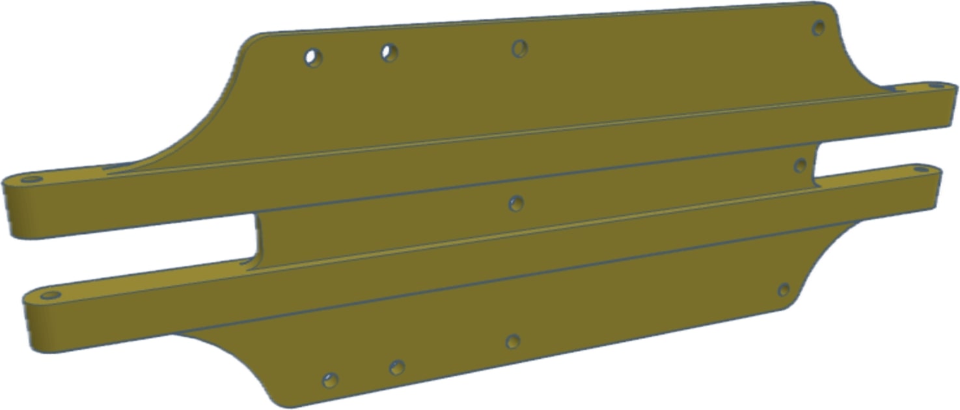
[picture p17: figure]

Figure 3.6: Frame part

## 3.5 Battery Case

A battery case (fig.3.7) supports the microcontroller and protects both the battery and the

converter.

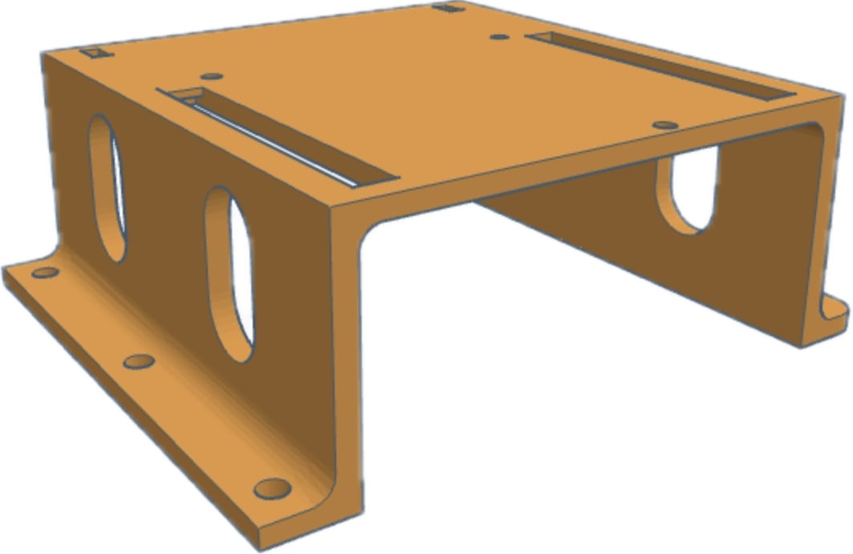
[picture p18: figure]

Figure 3.7: Battery case

## 3.6 Reaction Wheel

To ensure that the bicycle remains balanced, the reaction wheel (fig.3.8) must have sufficient

momentum of inertia to counteract the torque generated by gravity acting on the bicycle. The equation for the moment of inertia of a body lying in two dimensions in the X-Y plane is given by:
IZ =

X

i

mir

2
i

(3.1)

Since the moment of inertia of a body is proportional to the square of the radial distance to the mass, the reaction wheel is designed so that most of its mass is concentrated at the outer edges. This increases the moment of inertia IZ.

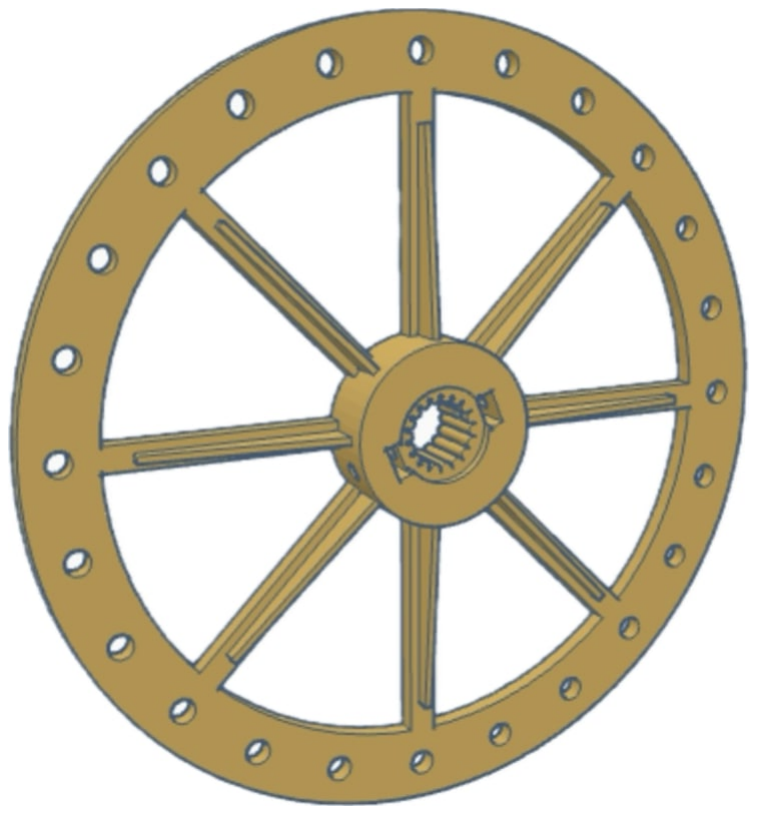
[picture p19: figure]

Figure 3.8: Reaction wheel

To achieve this weight distribution and allow for easy adjustments to the moment of inertia, a 3D-printed design was chosen, where the majority of the mass comes from a combination of M4 screws and nuts. This design provides flexibility in varying the moment of inertia by changing the position or number of screws and nuts.

# 4 Wirings

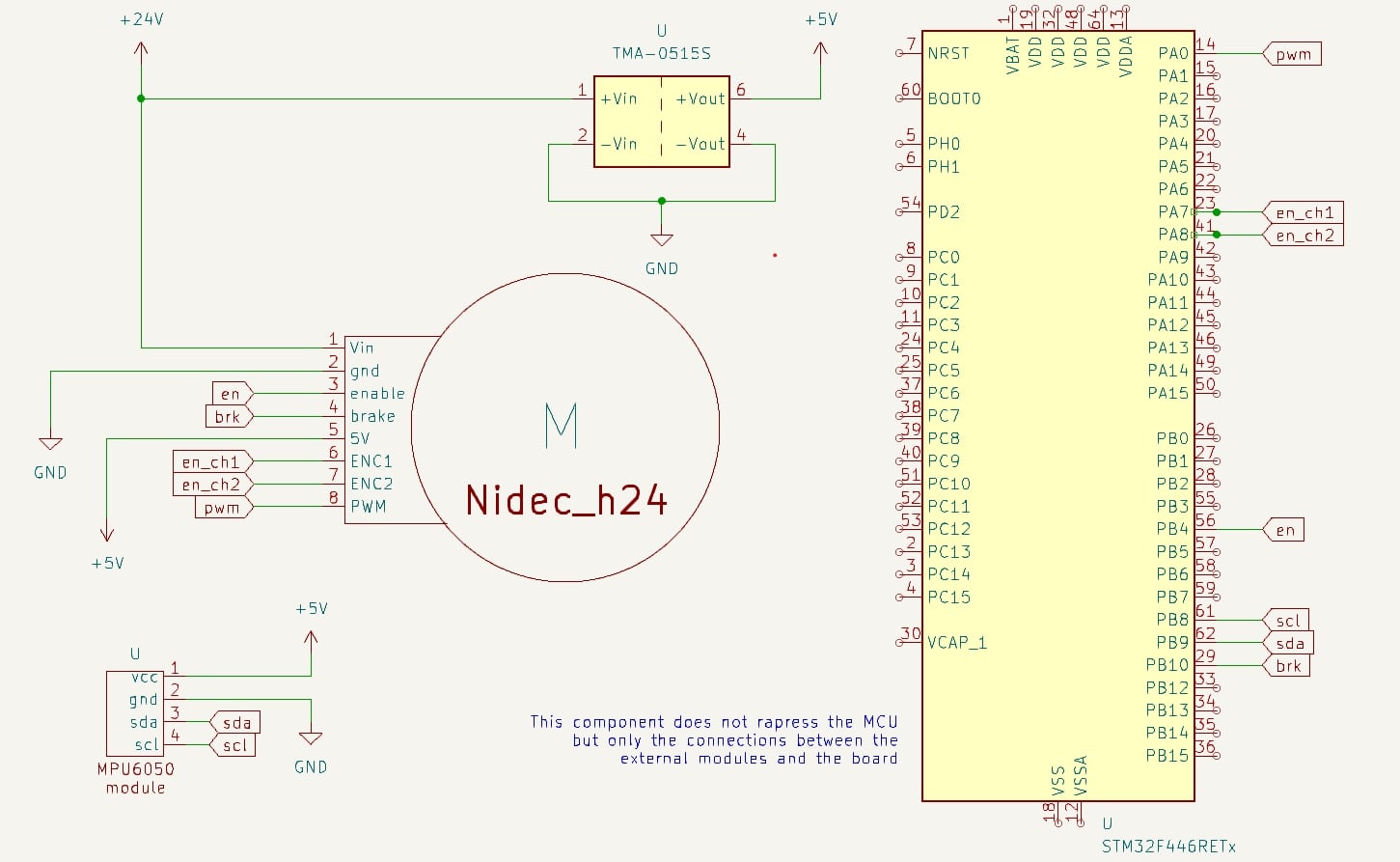
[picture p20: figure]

Figure 4.1: schematic

Brake PWM Direction ChA ChB SDA SCL

Arduino | D5 | A0 | D6 | D7 | D8 | D14 | D15
Morpho | PB4 | PA0 | PB10 | PA8 | PA9 | PB9 | PB8

Table 4.1: Peripherals connection to the microcontroller

1 | 2 | 3 | 4 | 5 | 6 | 7 | 8

24V GND Brake PWM Direction 5V ChA ChB

Table 4.2: Motor pinout

14

Pin | Function
1 | Motor supply voltage, 9V-24V.
2 | Supply ground.
3 | Brake: Vhigh = 2.0V to 5.0V = OFF, Vlow ≤ 0.15V = ON (motor stop).
4 | PWM = 20 kHz to 30 kHz; Vlow ≤ 0.6V, Vhigh = 2.0V to 5.0V, duty cycle = 20% to 100%.
5 | Vhigh = 2.0V to 5.0V or OPEN = Clockwise, Vlow ≤ 0.15V = Counter-clockwise.
6 | Standard = No connection. Encoder option = Logic supply, 5V ± 0.5V.
7 | Standard = Open-drain tachometer, six pulses per revolution, IC(max)=3.0mA. Encoder option = Channel A output: 90° phase tracking, 100 pulses per revolution, HIGH = 5V, LOW = 0V.
8 | Standard = No connection. Encoder option = Channel B output: 90° phase tracking, 100 pulses per revolution, HIGH = 5V, LOW = 0V.

Table 4.3: Pinout and function description of the motor driver

A shield (fig.4.4) is used to solder components, ensuring more stable connections and enhancing

modularity. This also makes the bicycle self-contained and streamlined, eliminating the clutter of wires and cables.

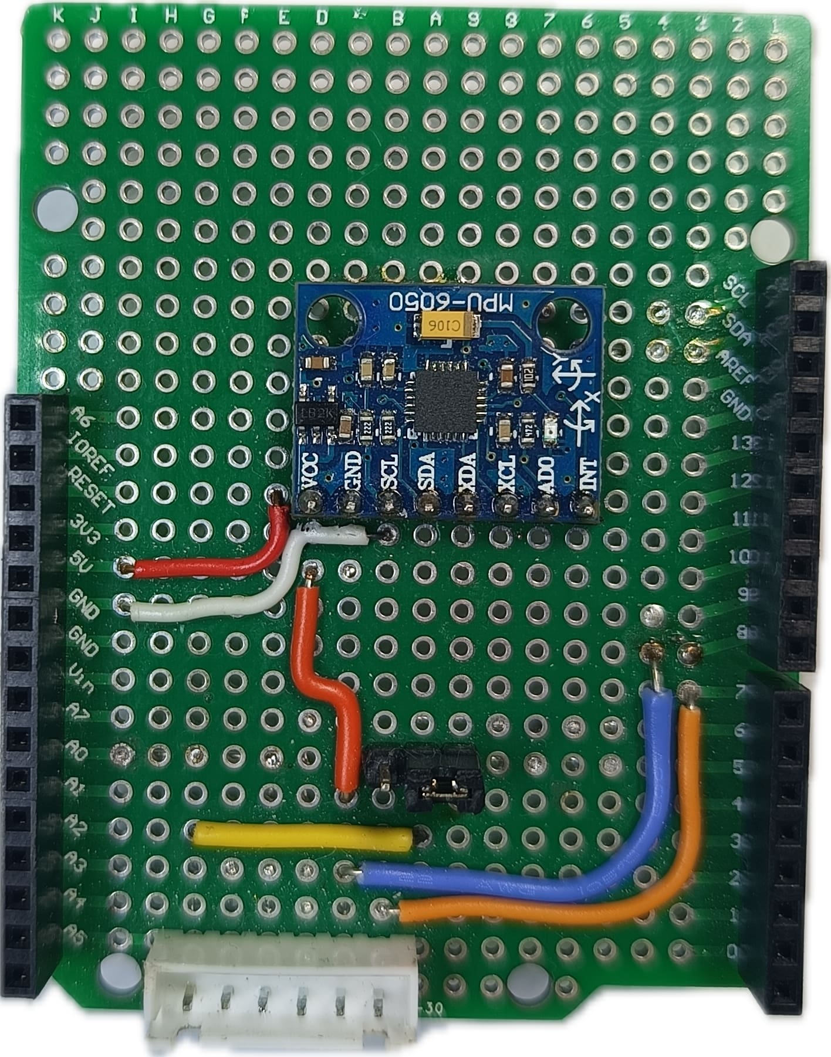
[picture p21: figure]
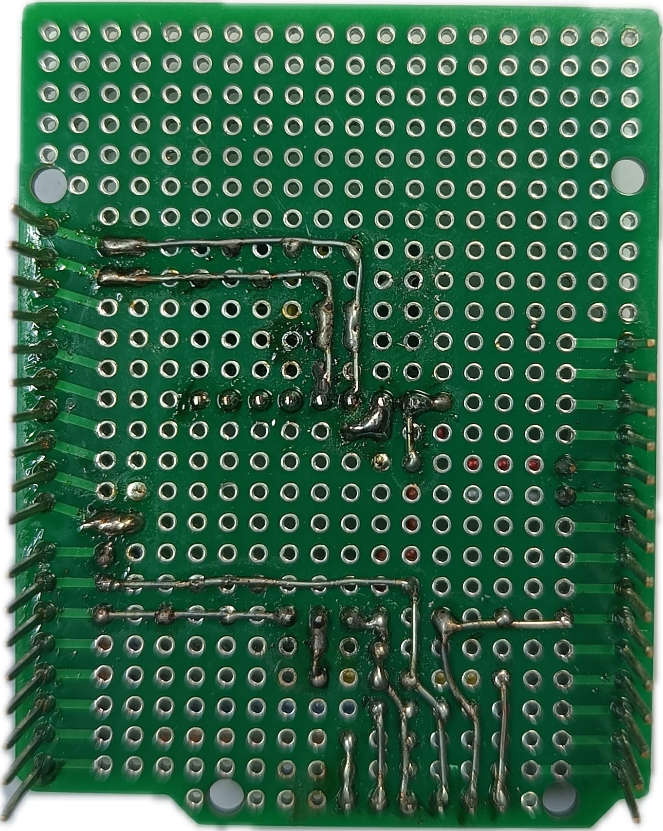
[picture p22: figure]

Figure 4.2: Shield: front | Figure 4.3: Shield: back

Figure 4.4: Shield

# 5 System’s control

To sample, Timer 2 counts up so that an interrupt is generated each time its counter reaches the ARR value. The control logic is implemented in the timer’s callback, which gets called by the interrupt’s handler.

PSC | ARR | fCLK | fs | Ts
TIM2 | 0 | 335999 84 MHz | 250 Hz | 4 ms

Table 5.1: Configuration of timer 2

The bicycle is an unstable system and tends to fall over very quickly. The control frequency depends on how fast the bicycle drops down and the effectiveness of the reaction wheel in correcting the fall. The control action needs to be fast relative to the system’s dynamics. Lower frequencies may not respond quickly enough to disturbances, while very high frequencies could introduce noise.

Firstly, a simple position control was tested. Specifically, a single PID was used, and the IMU reading provided the feedback that closed the loop. This control proved ineffective as strong oscillations prevented the system from reaching equilibrium. In particular, the actuation variable (which generates the PWM) did not allow for direct control of the motor’s speed.

Then, we decided to leverage the motor’s integrated encoder by creating a cascade control system. With an inner loop handling the speed control of the motor, while an outer loop performed the position control for the plant. The innermost PID was tuned so that the controlled system could follow a specific setpoint (several tests were conducted, including the tracking of a sine-wave) (fig: 5.2).

Another PID was initially used for the outer control too, but this caused some issues. Although oscillations decreased with the introduction of a cascade control, the bike’s balance could not be maintained. Moreover, it was complex to finely tune and synchronize the parameters of the two controllers.

When the reaction wheel rotates, it generates a torque, which is given by the product of the inertia of the reaction and its acceleration:

τ = I · α | (5.1)

16

This acceleration generates the lateral force that moves the body, which will depend on the height of the center of mass with respect to the ground:

FL =

τ
h

(5.2)

We concluded that the input setpoint speed, regardless of the tilt angle, should never be constant in order to generate a centripetal force that moves the bike. One technique could be to continuously increase (or decrease) the acceleration to reduce the error in the outer loop.

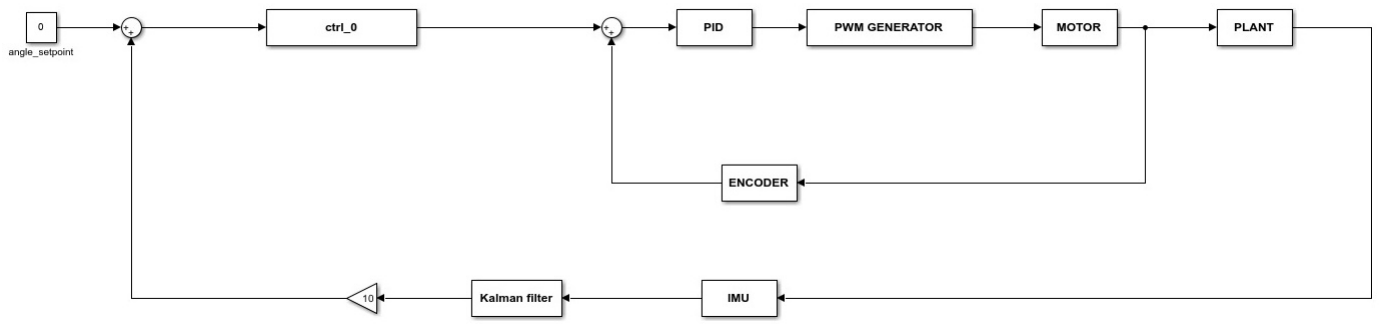
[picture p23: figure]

Figure 5.1: Control Loop

## 5.1 PID

The PID regulator has been chosen thanks to its capabilities to stabilize systems and to impose certain constraints:

- The proportional component decreases the rise time and reduces the steady-state error.

However, it may cause overshoot in the response. It adjusts the proportionality based on how far the bike is tilted.

- The integral contribution shortens the rise time and eliminates long-term errors, but it

increases the peak overshoot and prolongs the settling time.

- The derivative term reduces the overshoot and the settling time. This means the tran-

sient state of the system will be more dampened, controlling the rate of change in tilt.

Several tests (fig: 5.2) have been performed to finely tune the parameters and obtain a satisfying

performance in terms of rapidity and stability, in the end we set up:

Kp | Ki | Kd
PID coefficients | 10 | 0.1 0.42

Table 5.2: PID constants after tuning

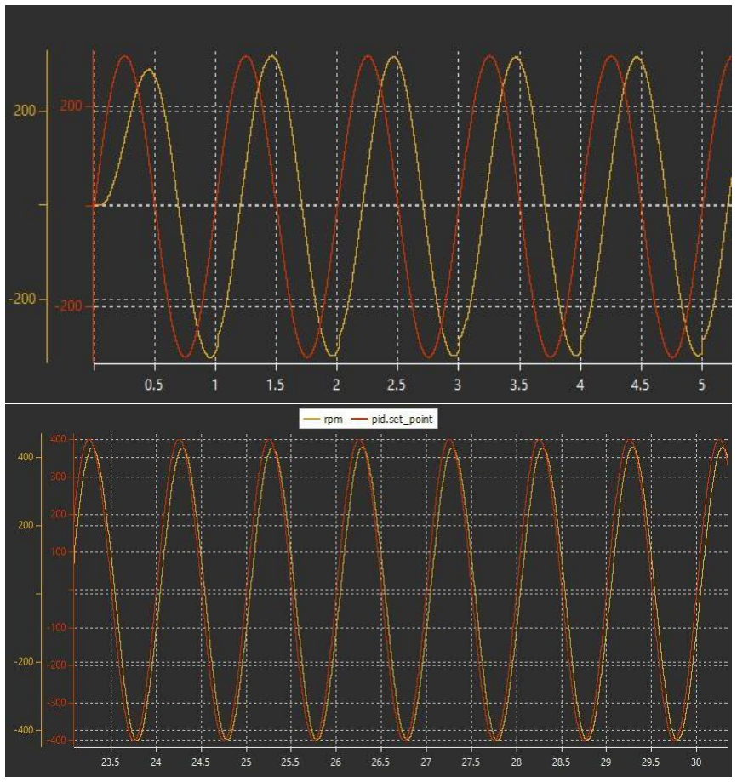
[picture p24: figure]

Figure 5.2: Pid test tuning

# 6 The most important parts of the Code

Code development and peripherals configuration are simplified with the STM32CubeIDE[3], an

integrated development environment that in combination with the STM32CubeMX provides a user-friendly graphical interface for peripheral setup. Developers benefit from tools for real-time debugging and performance optimization. The software ecosystem includes HAL (Hardware Abstraction Layer) and LL (Low-Layer) libraries, along with example projects provided by

STMicroelectronics, accelerating prototyping and development.

## 6.1 MPU6050 library

The IMU library has been developed in order to allow the return of data from the gyroscope and accelerometer; to do this, after an initial configuration phase, we just had to understand where the data was saved, create a data buffer and fill it with the raw data (using the I2C protocol and the HAL). The IMU was then calibrated by calculating the gyroscope bias, which

was subtracted from the calculation of the readings.

Listing 6.1: All data reading MPU6050

mpu_data mpu6050_data () {

uint8_t buffer [14];

HAL_I2C_Mem_Read (& hi2c1 , IMU_ADDR , ACCEL_XOUT_H_REG , I2C_MEMADD_SIZE_8BIT ,

buffer , 14 , 100) ;

mpu_data data ;
data . ax = ( float ) ( int16_t ) ( buffer [0] << 8 | buffer [1]) / ACC_SCALE ;
data . ay = ( float ) ( int16_t ) ( buffer [2] << 8 | buffer [3]) / ACC_SCALE ;
data . az = ( float ) ( int16_t ) ( buffer [4] << 8 | buffer [5]) / ACC_SCALE ;
data . gx = ( float ) ( int16_t ) (( buffer [8] << 8 | buffer [9]) - gx_bias )

/ GYRO_SCALE ;

data . gy = ( float ) ( int16_t ) (( buffer [10] << 8 | buffer [11]) - gy_bias )

/ GYRO_SCALE ;

data . gz = ( float ) ( int16_t ) (( buffer [12] << 8 | buffer [13]) - gz_bias )

/ GYRO_SCALE ;

return data ;

}

The code above highlights the structure used to collect the data (mpu data) starting from the base address ACCEL XOUT H REG of the MPU6050.

## 6.2 Nidec h24 motor library

The Nidec library allows the motor to be driven, in a clockwise or counterclockwise motion, depending on the modv input. We also specified a maximum value to limit the motor and a brake to activate or deactivate it. The timer was used to control the speed by comparing the out ccr to the ARR value. The mapping for calculating the out ccr is done with another specific

19 function within the library itself that allows the range of the input variable to be changed. The main library function is the following:

Listing 6.2: To make the motor turn based on the input

1 void nidec_h24_Move ( float modv , float max_modv , uint8_t brk ) {

2
3 | if ( brk == 0) {
4 | // brk -> 0: brakes
5 | HAL_GPIO_WritePin ( BRAKE_PORT , BRAKE_PIN , GPIO_PIN_RESET );
6 | TIM5 -> CCR1 = 0;
7 | }

8
9 | else {
10 | HAL_GPIO_WritePin ( BRAKE_PORT , BRAKE_PIN , GPIO_PIN_SET );

11
12 | if ( modv > 0) {
13 | // counter - clockwise
14 | HAL_GPIO_WritePin ( DIRECTION_PORT , DIRECTION_PIN , GPIO_PIN_SET );
15 | out_ccr = map ( modv , 0 , max_modv , 3938 , 0) ;
16 | } else {
17 | // clockwise
18 | HAL_GPIO_WritePin ( DIRECTION_PORT , DIRECTION_PIN , GPIO_PIN_RESET );
19 | out_ccr = map ( modv , 0 , - max_modv , 3938 , 0) ;
20 | }

21
22 | if ( out_ccr > 0 && out_ccr < htim5 . Instance -> ARR )
23 | TIM5 -> CCR1 = out_ccr ;
24 | else
25 | TIM5 -> CCR1 = 0;

26
27 | // Generate an update event to reload the value immediately
28 | }

29

30 }

## 6.3 Encoder library

The encoder is used for speed sensing which will be used for the inner PID control action.

Listing 6.3: Encoder Update

1 | inline static void __encoder_update ( encoder_t *e ) {
2 | uint32_t cur_cnt ;
3 | int32_t diff , cur_velocity ;

4
5 | cur_cnt = e -> tim -> Instance - > CNT ;

6
7 | // Handle overflow and underflow
8 | if ( __HAL_TIM_IS_TIM_COUNTING_DOWN (e -> tim ) ) {
9 | if (( uint32_t ) cur_cnt < ( uint32_t )e -> last_count ) // underflow
10 | diff = ( uint32_t )e -> last_count - ( uint32_t ) cur_cnt ;
11 | else

diff = (( uint32_t )e -> tim -> Instance -> ARR - ( uint32_t ) cur_cnt ) + ( uint32_t )e ->

last_count ;
} else {

if ( cur_cnt > e - > last_count ) // overflow

diff = ( uint32_t )e -> last_count - ( uint32_t ) cur_cnt ;

else
diff = (( uint32_t )e -> tim -> Instance -> ARR - ( uint32_t )e -> last_count ) + ( uint32_t )

cur_cnt ;

}

// velocity in pulses per second

if (( uint32_t )e -> last_count == ( uint32_t ) cur_cnt )

diff = 0;

cur_velocity = ( float ) diff / DT_enc / ( float ) e -> resolution ;

// Filtering velocity

e -> velocity_pps = BETA * e -> velocity_pps + (1.0 - BETA ) * cur_velocity ;

e -> last_count = cur_cnt ;

}

The main function of the implemented library reads the current timer count, calculates the difference from the previous count by handling overflow and underflow cases, and then calculates the rate in pulses per second.

## 6.4 Main control

In the main code, all the declarations of variables and structures have been placed; the functions related to peripherals, timers and so on, were initialized there too. The advantage of using timers is that we know precisely the time intervals of the various instructions as they are started within the callback function with jumps in the code if an interrupt is detected.
In our case the main callback is presented like this:

Listing 6.4: Period Elapsed Callback in the Main code

if ( htim -> Instance == TIM2 ) {

data = mpu6050_data () ;

new_angle = - atan ( data . ax / sqrt ( data . ay * data . ay + data . az * data . az ) )

* 180 / M_PI ;

kalmanUpdate (& filter , data .gy , new_angle );

pitch_angle = filter . angle - angle_offset ;

distance = -10 * pitch_angle ;

distance_error = distance_setpoint - distance ;

if ( distance_error < distance_setpoint ) {

distance_setpoint -= weight_balance * dt ;

} else {

distance_setpoint += weight_balance * dt ;

}

rpm = fabs ( encoder_get_pps (& enc ));

if ( pid_out < 0 && rpm > 700)

distance_setpoint -= rpm_limit ;

if ( pid_out > 0 && rpm > 700)

distance_setpoint += rpm_limit ;

pid_set_setpoint (& pid , distance_setpoint );

if ( pitch_angle < -20 || pitch_angle > 20) {

distance_setpoint = 0;
nidec_h24_Move (0 , 0, 0) ;

pid_reset (& pid ) ;

} else {

pid_out = pid_compute_control_action (& pid , distance );

nidec_h24_Move ( pid_out , 450 , 1) ;

}

}

Firstly, the data are read from the IMU, then the Kalman filter gets updated. The position error with respect to the setpoint is calculated and then re-calibrated, the data from the encoder, whose frequency is much higher than the external position loop, is taken. Finally the PID is intervened to set a PWM reference for the motor.

# 7 Tests and Results

This section covers all the tests and results obtained during the design process. They are discussed in a qualitative manner, based on graphs from measuring instruments and the SWD Data Trace Timeline Graph tool from the STM32CubeIDE.

## 7.1 Complementary Filter Test

To assess the performance of the balancing algorithm, first of all we measured the tilt angle of the bike to ensure the readings were accurate.

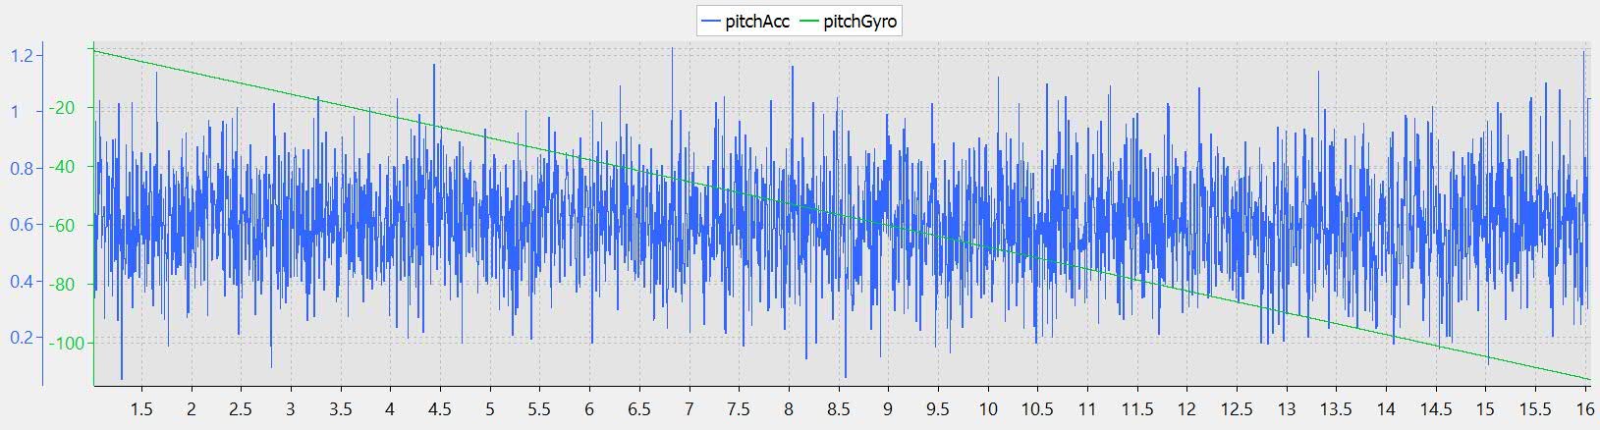
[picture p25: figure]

Figure 7.1: Raw pitch readings

As expected, the integration of the gyroscope contribution tends to increase; with rotation rate integration, the error on the angle gets higher, because it sums previous errors. We then processed this raw lean data (see fig.7.1) using a complementary filter to confirm the data’s

consistency and accuracy.

As shown in 7.2, 7.3 and 7.4, the filtered angle effectively smooths out fluctuations in the raw pitch data, removing sudden changes in the angle. This illustrates the effectiveness of our complementary filter in providing a stable readout.

23

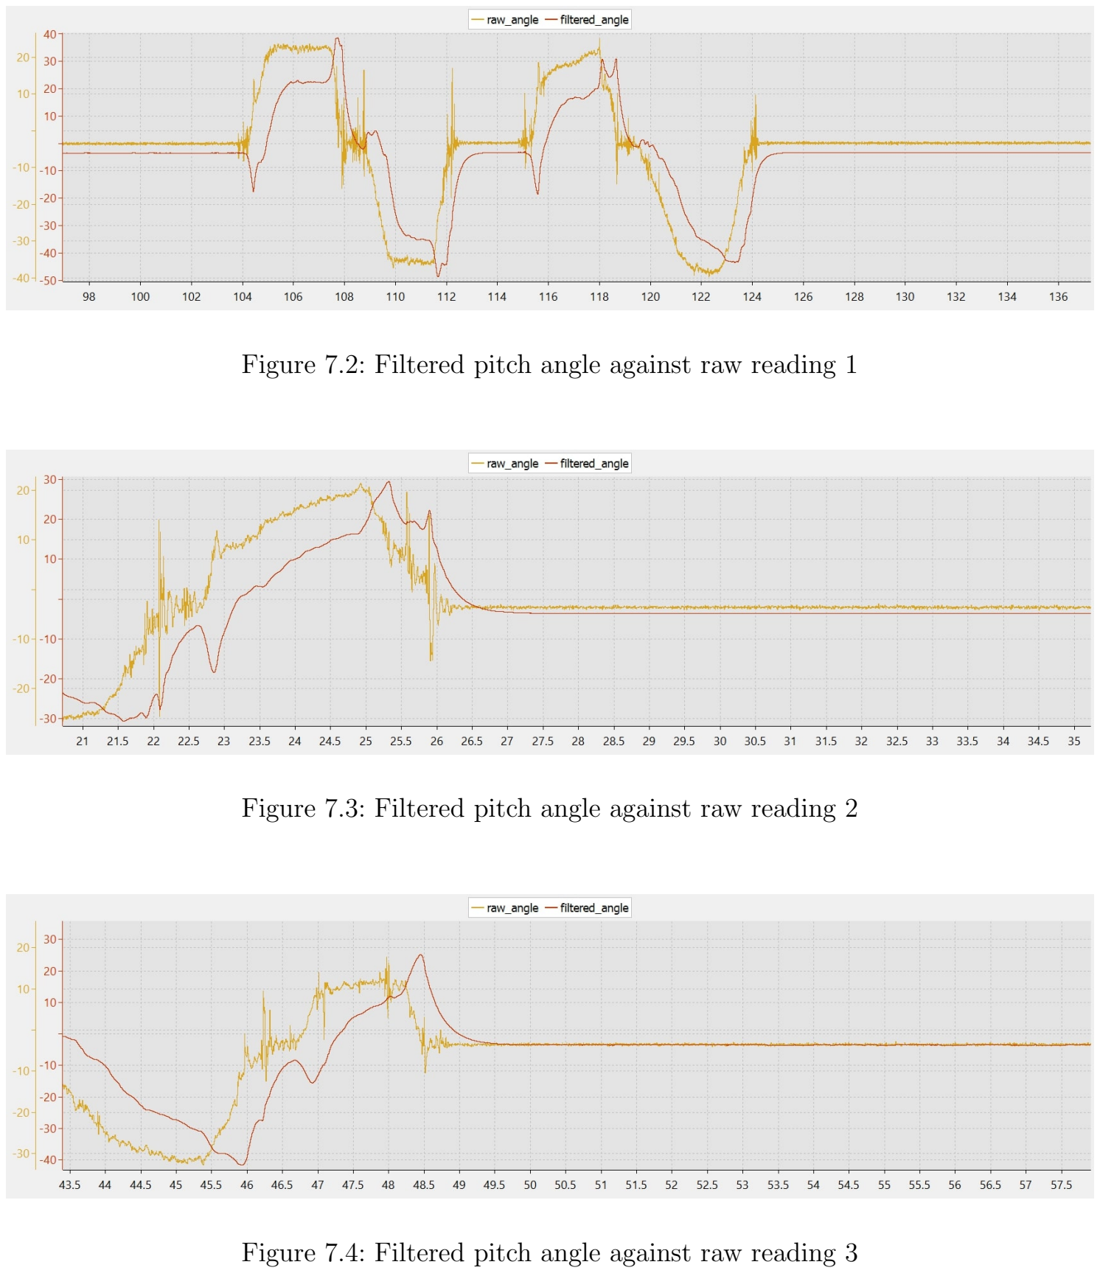
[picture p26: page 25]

Figure 7.2: Filtered pitch angle against raw reading 1

Figure 7.3: Filtered pitch angle against raw reading 2

Figure 7.4: Filtered pitch angle against raw reading 3

## 7.2 Kalman Filter Comparison

As we discussed in the chapter 2.4.2, Kalman filter has allowed us to obtain better results and here is a brief comparison of the results obtained.

In the following figures 7.5 and 7.6, the yellow signal was the angle estimation obtaines through the Kalman filter, while the red one was derived with the complementary:


Figure 7.5: Kalman filter vs complementary filter 1


Figure 7.6: Kalman filter vs complementary filter 2

## 7.3 PWM Signal Verification

To verify the effective generation of the PWM signal, we utilized an oscilloscope. The measurement instrument confirmed that the signal maintains the specified frequency and pulse characteristics.


Figure 7.7: PWM signal with a 20% duty cycle

As shown in Figure 7.7, the signal exhibits a duty cycle of 20%. The voltage alternates between

3.33V and 0V, consistent with expectations for this duty cycle.


Figure 7.8: PWM signal with a 80% duty cycle

Similarly, Figure 7.8 shows the PWM signal at a 80% duty cycle. In each case, the oscilloscope

measurements confirmed the expected behavior of the signal.

## 7.4 Encoder Signals Verification


Figure 7.9: Encoder channels

Figure 7.9 displays in blue Channel A and in yellow Channel B. The signals are squared waveforms shifted of 90 degrees.

# 8 Conclusions and future developments

To conclude, the control system, based on two feedback loop, the inner one for speed and the outer one for position, ensures precise system management. The sensor fusion of data from an MPU6050 IMU, using a Kalman filter, provided accurate angle measurements, allowing for effective stabilization even under changing conditions.

The system demonstrated a remarkable ability to maintain balance despite external disturbances and small changes in tilt, showing the effectiveness of the implemented control. However, there could be some improvement and potential future developments to make the system even more complete.

A possible improvement to the project could involve enabling it to move through space while maintaining balance. This would require the addition of a servo motor for steering and an additional motor for propulsion. Furthermore, a remote control module would be necessary for distance control. These updates would entail modifying the structure.

It would also be interesting to test different control approaches, such as implementing a predictive control system, to make a comparison.

28

# List of Figures

2.1 STM32 NUCLEO-F446RE | | 4
2.2 Motor | | 5
2.3 Motor encoder | | 6
2.4 IMU MPU6050 | | 7
2.5 DC-DC buck converter | | 9
2.6 Lipo battery | | 9
3.1 3d model Solidworks | 10
3.2 3D printed bike | 11
3.3 Wheel | 11
3.4 Bearing | 11
3.5 Wheel and bearing | 11
3.6 Frame part | 12
3.7 Battery case | 12
3.8 Reaction wheel | 13
4.1 schematic | 14
4.2 Shield: front | 15
4.3 Shield: back | 15
4.4 Shield | 15
5.1 Control Loop | 17
5.2 Pid test tuning | 18
7.1 Raw pitch readings | 23
7.2 Filtered pitch angle against raw reading 1 | 24
7.3 Filtered pitch angle against raw reading 2 | 24
7.4 Filtered pitch angle against raw reading 3 | 24
7.5 Kalman filter vs complementary filter 1 | 25
7.6 Kalman filter vs complementary filter 2 | 25
7.7 PWM signal with a 20% duty cycle | 26
7.8 PWM signal with a 80% duty cycle | 26
7.9 Encoder channels | 27

29

# List of Tables

2.1 Configuration of timer 5 | | 5
2.2 Configuration of the timer 1 | | 6
2.3 Filters advantages | | 8
4.1 Peripherals connection to the microcontroller | 14
4.2 Motor pinout | 14
4.3 Pinout and function description of the motor driver | 15
5.1 Configuration of timer 2 | 16
5.2 PID constants after tuning | 18

30

# Bibliography

[1] Github repository. Last access date: 21 Nov 2024. url: https://github.com/Phersax/

Self-balancing-bike. (https://github.com/Phersax/Self-balancing-bike)

[2] SolidWorks. Last access date: 21 Nov 2024. url: https://www.solidworks.com/.
[3] STM32IDE. Last access date: 21 Nov 2024. url: https://www.st.com/en/development-

tools/stm32cubeide.html. (https://www.st.com/en/development-tools/stm32cubeide.html)

31

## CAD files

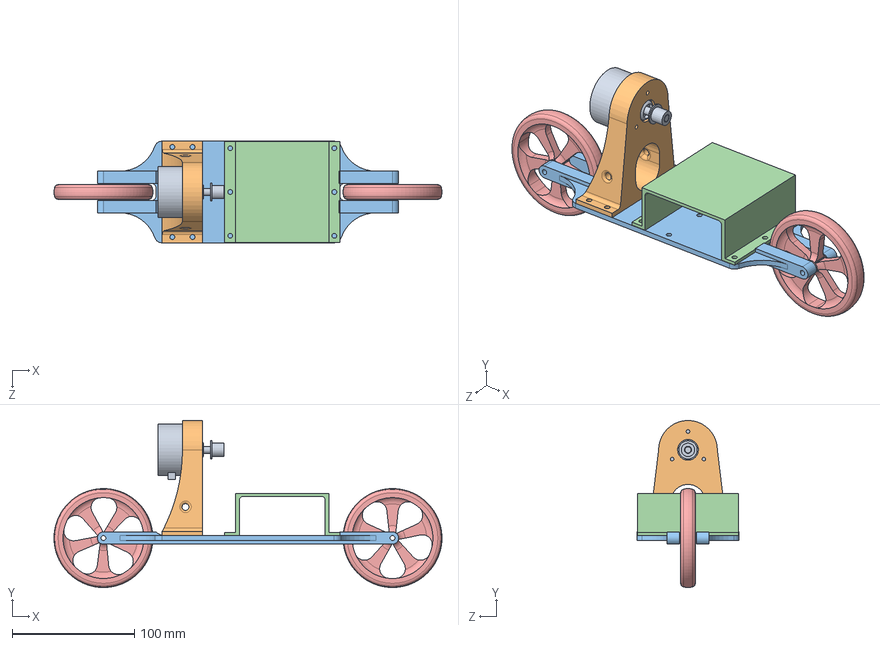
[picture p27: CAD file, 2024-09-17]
3D_model/assembly.SLDASM
316.8 x 136.4 x 83.0 mm
wheel_part x 2
battery_case_part
frame_part
support_motor_part
nidech24_part

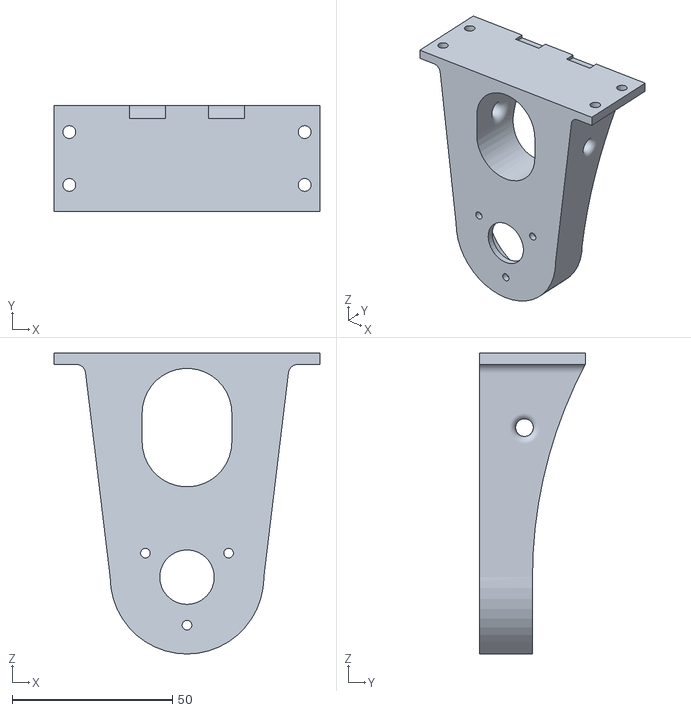
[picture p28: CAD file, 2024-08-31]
3D_model/printable_parts/support_motor_part_v2.STL
83.0 x 33.0 x 94.0

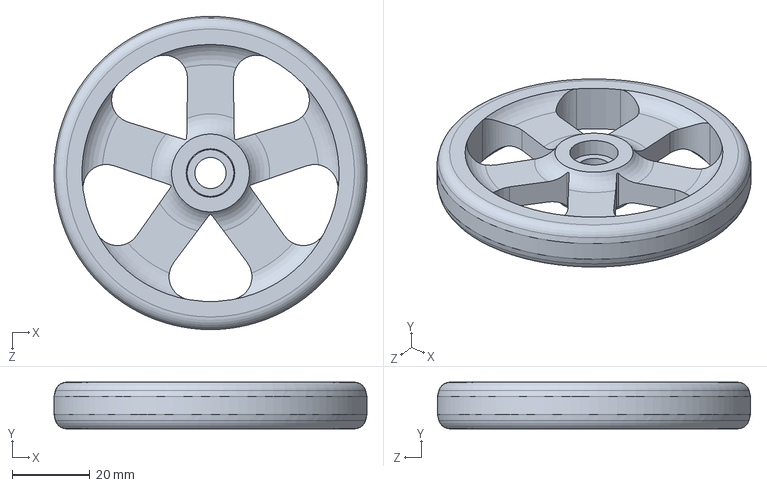
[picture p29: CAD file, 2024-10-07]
3D_model/wheel_bearings_part_v3.SLDPRT
80.4 x 12.0 x 80.4 mm

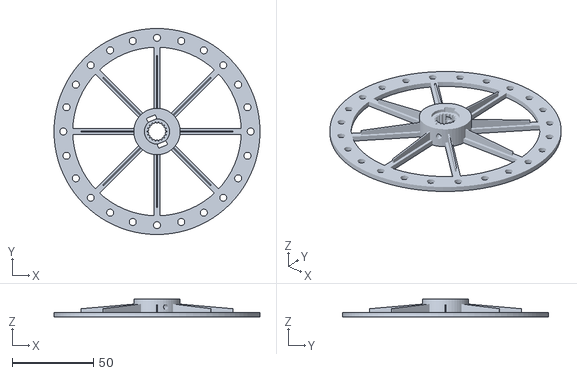
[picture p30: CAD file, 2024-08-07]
3D_model/printable_parts/rw_bike_reaction_wheel_1x.stl
126.4 x 126.4 x 11.0

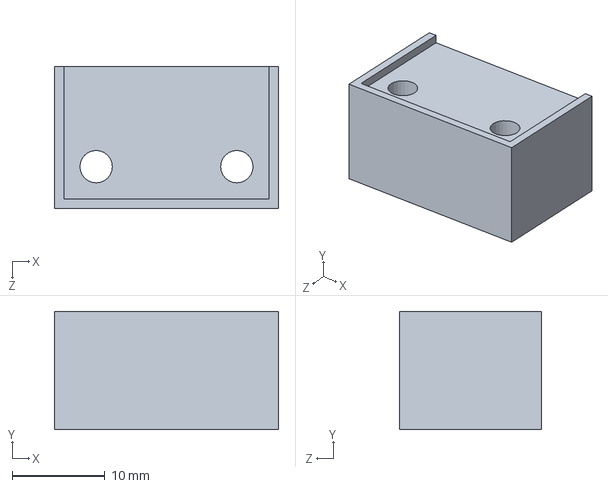
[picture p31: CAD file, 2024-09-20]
3D_model/support_mpu6050_part.SLDPRT
24.2 x 12.8 x 15.3 mm

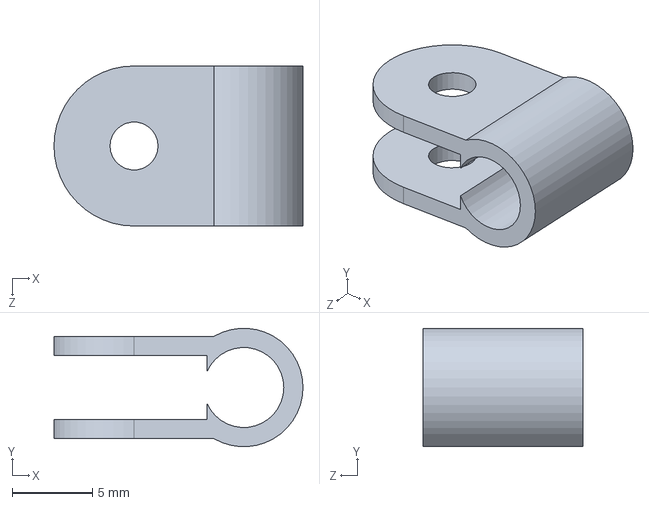
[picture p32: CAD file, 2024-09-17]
3D_model/support_wire_part1.SLDPRT
15.6 x 7.38 x 10.0 mm

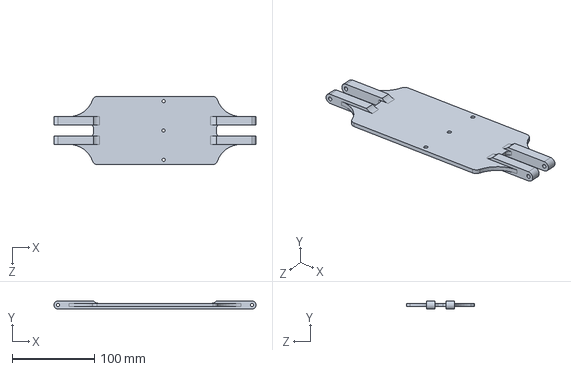
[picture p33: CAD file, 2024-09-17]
3D_model/frame_part.SLDPRT
246.0 x 10.0 x 83.0 mm

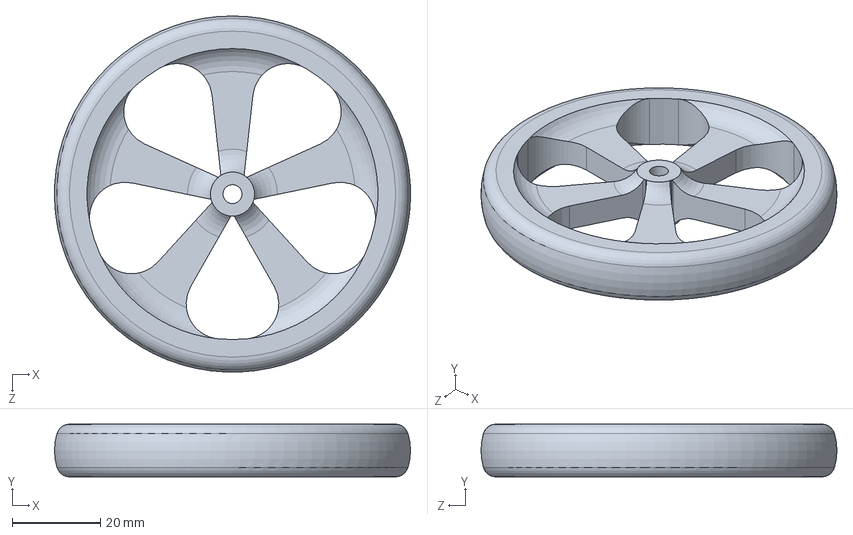
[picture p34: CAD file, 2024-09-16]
3D_model/wheel_part.SLDPRT
80.8 x 12.0 x 80.8 mm

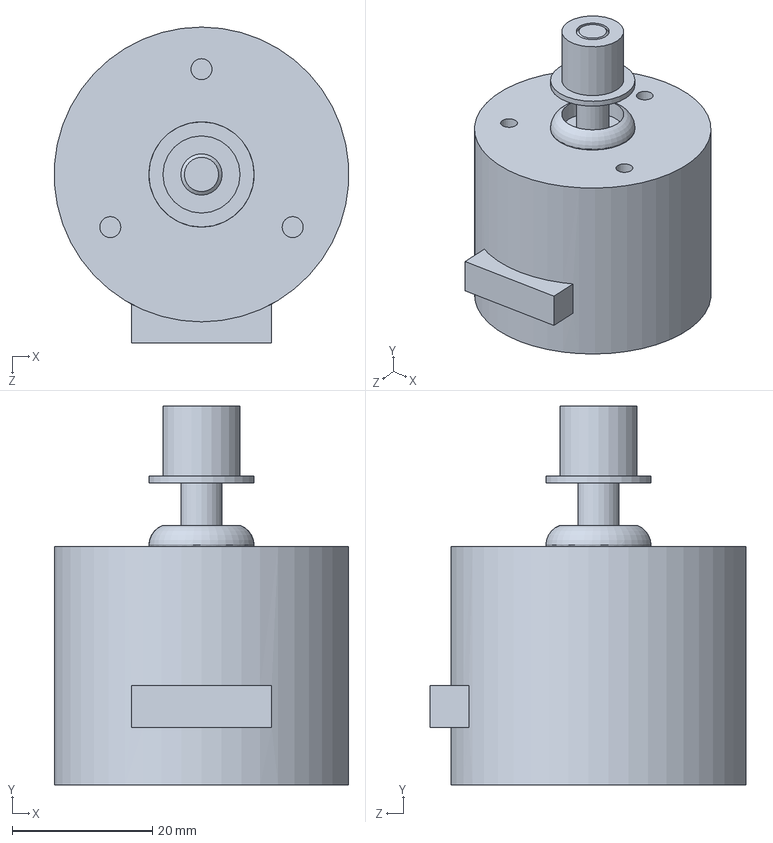
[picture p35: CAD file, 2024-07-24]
3D_model/nidech24_part.SLDPRT
41.9 x 54.0 x 45.0 mm

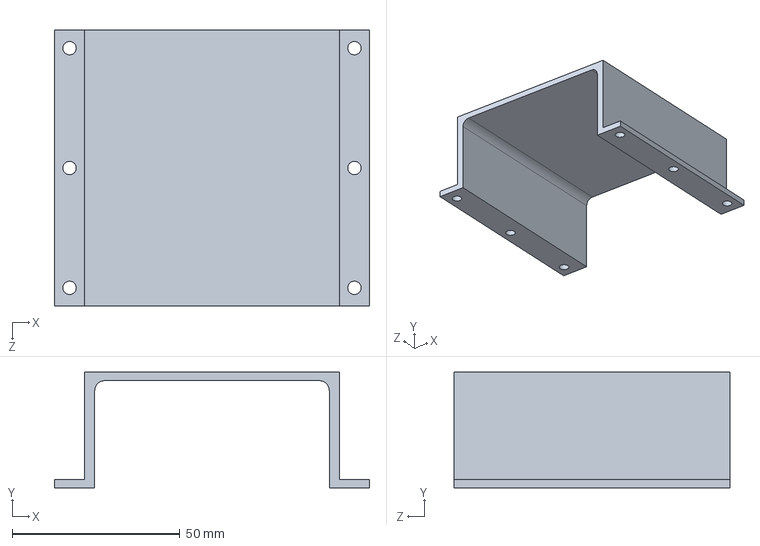
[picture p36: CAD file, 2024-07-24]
3D_model/battery_case_part.SLDPRT
94.0 x 34.5 x 82.5 mm

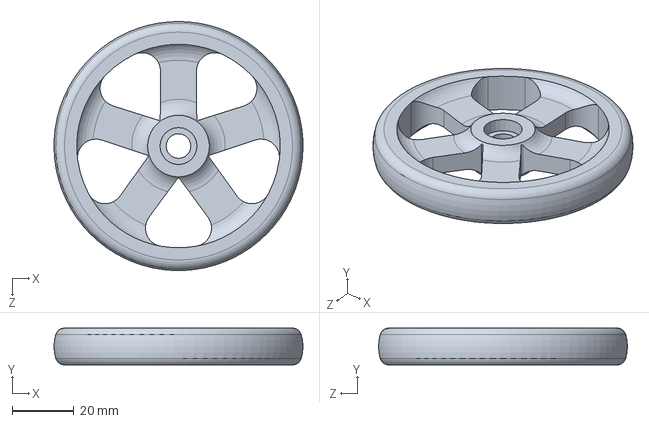
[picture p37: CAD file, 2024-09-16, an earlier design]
3D_model/wheel_bearings_part.SLDPRT
80.8 x 12.0 x 80.8 mm

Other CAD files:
3D_model/support_wire_part2.SLDPRT
3D_model/support_motor_part.SLDPRT
3D_model/inertial_wheel_part.SLDPRT
3D_model/wheel_bearings_part_v2.SLDPRT
3D_model/printable_parts/battery_case_part.STL
3D_model/printable_parts/frame_part.STL
3D_model/printable_parts/support_motor_part.STL
3D_model/printable_parts/support_mpu6050_part.STL
3D_model/printable_parts/support_wire_part1.STL
3D_model/printable_parts/support_wire_part2.STL
3D_model/printable_parts/wheel_bearings_part.STL
3D_model/printable_parts/wheel_bearings_part_v2.STL
3D_model/printable_parts/wheel_bearings_part_v3.STL
3D_model/printable_parts/wheel_part.STL

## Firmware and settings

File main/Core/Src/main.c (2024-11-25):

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
/* Includes ------------------------------------------------------------------*/
#include "main.h"
#include "i2c.h"
#include "tim.h"
#include "gpio.h"

/* USER CODE BEGIN Includes */
#include <stdio.h>
#include <stdint.h>
#include "encoder.h"
#include "mpu6050.h"
#include "kalman_filter.h"
#include "nidec_h24.h"
#include "pid.h"
#include <math.h>
/* USER CODE END Includes */


/* USER CODE BEGIN PV */

//encoder
static encoder_t enc;
static float rpm;

//IMU
static float distance, distance_error, distance_setpoint, new_angle, pid_out;
static mpu_data data;
static HAL_StatusTypeDef status;

//controllers
static PID_t pid;
static float Kp = 9.2;
static float Ki = 0.6;
static float Kd = 0.25;

//Control variables
static float rpm_limit = 0.03;
static float weight_balance = 5;
static float set_point = 0;
static float max_pid = 450;

//kalman
static float in_angle;
static Kalman filter;
static float angle_offset = -2.3;
static float pitch_angle;

//sampling time timer2
static float dt;

//prototype to get the dt
float getDt(TIM_HandleTypeDef *htim);

/* USER CODE END PV */

void SystemClock_Config(void);
/**
  * @brief  The application entry point.
  * @retval int
  */
int main(void)
{

  /* MCU Configuration--------------------------------------------------------*/

  /* Reset of all peripherals, Initializes the Flash interface and the Systick. */
  HAL_Init();

  /* Configure the system clock */
  SystemClock_Config();

  /* Initialize all configured peripherals */
  MX_GPIO_Init();
  MX_TIM5_Init();
  MX_I2C1_Init();
  MX_TIM1_Init();
  MX_TIM2_Init();
  /* USER CODE BEGIN 2 */

	//compute dt of timer2
	dt = getDt(&htim2);

	//pid config
	pid_init(&pid, Kp, Ki, Kd, -max_pid, max_pid, 150, -150);
	pid_set_setpoint(&pid, set_point);

	//imu init
	status = mpu6050_init();

	data = mpu6050_data(); //achieve the initial angle for the kalman filter

	in_angle = -atan(data.ax / sqrt(data.ay * data.ay + data.az * data.az))* 180 / M_PI;

	// Kalman filter init
	kalman_init(&filter, in_angle ); //set the initial angle

	//motor init
	nidec_h24_init();

	//encoder init
	encoder_init(&enc, AB, &htim1, 100);

	//notifies the term of initialization
	for (int i=0; i<6;i++){
		HAL_Delay(500);
		HAL_GPIO_TogglePin(GPIOA, GPIO_PIN_5);
	}

	//the timer2 starts
	HAL_TIM_Base_Start_IT(&htim2);
  /* USER CODE END 2 */

  /* Infinite loop */
  /* USER CODE BEGIN WHILE */
	while (1) {

		HAL_Delay(1);
    /* USER CODE END WHILE */

    /* USER CODE BEGIN 3 */
	}
  /* USER CODE END 3 */
}

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
/* USER CODE BEGIN 4 */

void HAL_TIM_PeriodElapsedCallback(TIM_HandleTypeDef *htim) {

	if (htim->Instance == TIM2) {



		data = mpu6050_data();

		new_angle = -atan(data.ax / sqrt(data.ay * data.ay + data.az * data.az))
				* 180 / M_PI;

		kalmanUpdate(&filter, data.gy, new_angle);


		pitch_angle = filter.angle - angle_offset;

		distance = -10 * pitch_angle;
		distance_error = distance_setpoint - distance;

		if (distance_error < distance_setpoint) {
			distance_setpoint -= weight_balance * dt;
		} else {
			distance_setpoint += weight_balance * dt;
		}

		rpm = fabs(encoder_get_pps(&enc));

		if (pid_out < 0 && rpm > 700)
			distance_setpoint -= rpm_limit;

		if (pid_out > 0 && rpm > 700)
			distance_setpoint += rpm_limit;

		pid_set_setpoint(&pid, distance_setpoint);

		if (pitch_angle < -20 || pitch_angle > 20) {
			distance_setpoint = 0;
			nidec_h24_Move(0, 0, 0);
			pid_reset(&pid);
		} else {
			pid_out = pid_compute_control_action(&pid, distance);
			nidec_h24_Move(pid_out, 450, 1);
		}
	}

}

float getDt(TIM_HandleTypeDef *htim) {
	if (htim->Instance == TIM2 || htim->Instance == TIM3
			|| htim->Instance == TIM4 || htim->Instance == TIM5
			|| htim->Instance == TIM6 || htim->Instance == TIM7)
		return (float) (((uint32_t) htim->Instance->ARR) + 1)
				* (((uint32_t) htim->Instance->PSC) + 1)
				/ ((uint32_t) HAL_RCC_GetPCLK1Freq() * 2);
	else
		return (float) (((uint32_t) htim->Instance->ARR) + 1)
				* (((uint32_t) htim->Instance->PSC) + 1)
				/ ((uint32_t) HAL_RCC_GetPCLK2Freq());
}
/* USER CODE END 4 */
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


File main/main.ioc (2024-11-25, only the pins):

Mcu.UserName=STM32F446RETx
PA0-WKUP.Signal=S_TIM5_CH1
PA13.Signal=SYS_JTMS-SWDIO
PA14.Signal=SYS_JTCK-SWCLK
PA5.GPIO_Label=LED
PA5.Signal=GPIO_Output
PA8.Signal=S_TIM1_CH1
PA9.Signal=S_TIM1_CH2
PB10.GPIO_Label=Direction
PB10.Signal=GPIO_Output
PB3.Signal=SYS_JTDO-SWO
PB8.Signal=I2C1_SCL
PB9.Signal=I2C1_SDA
PH0-OSC_IN.Signal=RCC_OSC_IN
PH1-OSC_OUT.Signal=RCC_OSC_OUT

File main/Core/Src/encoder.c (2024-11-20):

#include "encoder.h"
#include "main.h"
#include <math.h>

HAL_StatusTypeDef encoder_init(encoder_t *e, channel ch, TIM_HandleTypeDef *htim, uint32_t ppr) {

	HAL_StatusTypeDef ret = HAL_OK;

	if (htim == NULL)
		return HAL_ERROR;

	e->tim = htim;
	htim->Instance->CNT = 0;
	ret = HAL_TIM_Encoder_Start(htim, ch);

	if (ret != HAL_OK)
		return ret;

	//if the encoder is in quadrature, the resolution is 4
	if (ch == A || ch == B)
		e->resolution = 2;
	else
		e->resolution = 4;

	e->velocity_pps = 0.0;
	e->last_count = htim->Instance->CNT;
	e->ppr = ppr;

	return ret;
}

inline static void __encoder_update(encoder_t *e) {
	uint32_t cur_cnt;
	int32_t diff, cur_velocity;

	cur_cnt = e->tim->Instance->CNT;

	// Handle overflow and underflow
	if (__HAL_TIM_IS_TIM_COUNTING_DOWN(e->tim)) {
		if ((uint32_t)cur_cnt < (uint32_t)e->last_count) // underflow
			diff = (uint32_t)e->last_count - (uint32_t)cur_cnt;
		else
			diff = ((uint32_t)e->tim->Instance->ARR - (uint32_t)cur_cnt) + (uint32_t)e->last_count;
	} else {
		if (cur_cnt > e->last_count) // overflow
			diff = (uint32_t)e->last_count - (uint32_t)cur_cnt;
		else
			diff = ((uint32_t)e->tim->Instance->ARR - (uint32_t)e->last_count) + (uint32_t)cur_cnt;
	}

	// velocity in pulses per second
	if ((uint32_t)e->last_count == (uint32_t)cur_cnt)
		diff = 0;

	cur_velocity = (float) diff / DT_enc / (float) e->resolution;

	// Filtering velocity
	e->velocity_pps = BETA * e->velocity_pps + (1.0 - BETA) * cur_velocity;
	e->last_count = cur_cnt;
}

float encoder_get_velocity_rps(encoder_t *e) {
	__encoder_update(e);
	return e->velocity_pps / (float) e->ppr;
}

float encoder_get_velocity_rpm(encoder_t *e) {
	return encoder_get_velocity_rps(e) * 60.0;
}

float encoder_get_pps(encoder_t *e) {
	__encoder_update(e);
	return e->velocity_pps;
}

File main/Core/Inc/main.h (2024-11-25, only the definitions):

#define LED_Pin GPIO_PIN_5
#define LED_GPIO_Port GPIOA
#define Direction_Pin GPIO_PIN_10
#define Direction_GPIO_Port GPIOB

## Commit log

2024-07-09 MPU6050 library
    Created new librerya for the mpu6050 module and performed tests using the STM32CubeIde SWV
    [mpu6050_test Debug.cfg]
2024-07-23 Start of the 3D model design
    [assembly.SLDASM, battery_case_part.SLDPRT, frame_part.SLDPRT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]
2024-07-24 bldc motor nidec h24 3d model
    -bldc motor nidec h24 3d model
    -upgrade solidworks parts
    -add stl file of the wheel
    [assembly.SLDASM, battery_case_part.SLDPRT, frame_part.SLDPRT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]
2024-07-27 Early motor driver implementations
    -potentiometer code for modify the duty cycle manually,
    -first lines for the motor pwm controller
2024-08-06 support motor part
    [assembly.SLDASM, frame_part.SLDPRT, support_motor_part.SLDPRT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]
2024-08-07 add 3d printable files
    [battery_case_part.STL, frame_part.STL, inertial_wheel_part.SLDPRT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]
2024-08-19 new printable parts
    [battery_case_part.STL, frame_part.STL, rw_bike_reaction_wheel_1x.stl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]
2024-08-24 LED blink
2024-08-25 PWM testing
2024-08-26 pwm test
2024-08-26 nidec_h24 library, pwm and direction testing
2024-08-27 final test motor
    [assembly.SLDASM, battery_case_part.SLDPRT, battery_case_part.STL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]
2024-08-31 mpu6050 + motor test
    [main_test Debug.cfg, mpu6050_test Debug.cfg]
2024-09-07 v0.2
    test with PID and debugging
2024-09-09 test on filter
    [mpu6050_test Debug.cfg]
2024-09-10 test about filter
2024-09-11 complementary filter for sensors fusion
2024-09-16 update 3D model
    [battery_case_part.SLDPRT, wheel_part.SLDPRT]
2024-09-16 stl files
    [nidech24_part.SLDPRT, wheel_bearings_part.SLDPRT, wheel_bearings_part.STL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]
2024-09-17 support wire printable files
    [assembly.SLDASM, frame_part.SLDPRT, support_wire_part1.SLDPRT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]
2024-09-20 support mpu6050 printable part
    [support_mpu6050_part.SLDPRT, support_mpu6050_part.STL]
2024-09-20 edit nidec h24 library
    set the angle action range
    edit nidec h24 library and add brake
2024-09-20 Maximizing pwm resolution (PSC and ARR setting)
2024-09-24 Encoder testing
2024-09-26 fix encoder
2024-09-26 Encoder library
2024-09-26 Create encoder library
2024-09-26 Complete encoder library upload
2024-09-27 Encoder loop-control
2024-09-28 test encoder
2024-09-28 trace log data from encoder, set BETA and DT
    [encoder_library Debug.cfg]
2024-09-29 data trace from SWV
2024-09-29 fix current counter encoder
    [encoder.c, main.c]
2024-09-29 PID tuning
2024-09-29 integration of the encoder library into the main
2024-09-29 2nd identification test
    [look_up_table.xlsx]
2024-09-30 kalman filter test
2024-09-30 integration of the kalman_filter into the main
    [wheel_bearings_part_v2.SLDPRT, wheel_bearings_part_v2.STL]
2024-10-04 fix bugs on mpu6050 library
    [main.c, mpu6050.c]
2024-10-07 wheels v3
    [wheel_bearings_part_v3.SLDPRT, wheel_bearings_part_v3.STL]
2024-10-10 gyroscope bias and rpm control
2024-11-20 Changes on main
    Stable version 1.0
    [encoder_library Debug.cfg, look_up_table.xlsx, main_test Debug.cfg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]
2024-11-25 notifies the term of initialization with led buit-in

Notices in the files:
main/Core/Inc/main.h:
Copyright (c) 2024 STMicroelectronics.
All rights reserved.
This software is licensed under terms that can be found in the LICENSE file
